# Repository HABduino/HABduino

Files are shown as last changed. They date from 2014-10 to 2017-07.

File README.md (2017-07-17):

## Habduino

This is the original code base for Habduino V4.X boards. It is still suitable for flights but is no longer maintained or supported. Hardware definitions are all current. 

This code provides simultaneous (where legal and supported by the hardware installed) transmission of radio telemetry via RTTY and APRS on Habduino Arduino addon boards for High Altitude Ballooning. 

## Move to Flextrack

We strongly recommend you move to Dave Akermans Flextrack as this is updated and maintained. The Flextrack code is here https://github.com/daveake/FlexTrack and has Habduino specific amendments.

## Disclaimer

The Habduino code is provided as is with no guarantees of performance or operation. 

If you decide to use this code under a balloon it’s your responsibility to ensure you comply with the local legislation and laws regarding meteorological balloon launching and radio transmission in the air. 
The Radiometrix NTX2B 434Mhz is NOT license exempt in the United States of America and does need a radio amateur license.

Use of APRS requires a radio amateur license in all countries and a number of countries don’t permit the airborne use of APRS under any circumstances. 

It is YOUR responsibility to ensure Habduino hardware and code is used safely and legally please review the safety section on the website. 

## Further Reading on High Altitude Ballooning

Please read this http://www.daveakerman.com/?p=1732

## License

The hardware design & code for Habduino is released under a Creative Commons License 3.0 Attribution-ShareAlike License : http://creativecommons.org/licenses/by-sa/3.0/

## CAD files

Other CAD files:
Hardware/HABdunio.skp

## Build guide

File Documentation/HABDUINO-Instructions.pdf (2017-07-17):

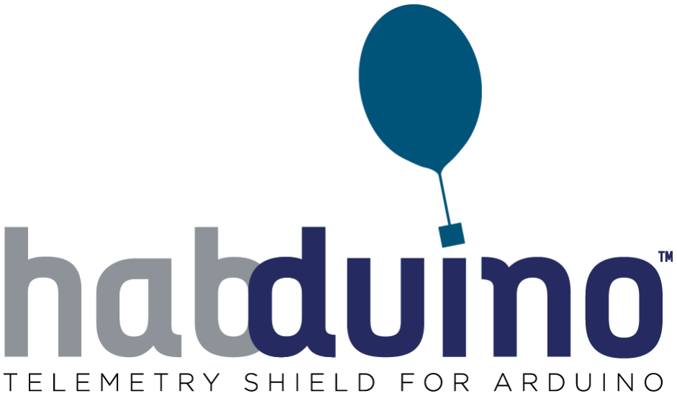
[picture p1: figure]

INSTRUCTION MANUAL

V1.2

Thanks for your purchase of the Habduino Shield.

The Habduino kit is sold as is with no guarantees of performance or operation.

If you decide to use this product under a balloon it’s your responsibility to ensure you comply with the local legislation and laws regarding meteorological balloon launching and radio transmission in the air.

The Radiometrix NTX2B 434Mhz is NOT license exempt in the United States of America and does need a radio amateur license.

Use of APRS requires a radio amateur license in all countries and a number of countries don’t permit the airborne use of APRS under any circumstances.

The Habduino cannot do APRS without an addon Radiometrix HX1 module (See APRS Section).

It is YOUR responsibility to ensure this kit is used safely please review the safety section.

Please read this guide on High Altitude Ballooning. http://www.daveakerman.com/?p=1732

Please note the where supplied RG174 pigtail MUST be turned into a suitable antenna. Instructions to do this are here : http://ukhas.org.uk/guides:payloadantenna

The hardware design & code for Habduino is released under a Creative Commons License 3.0 Attribution-ShareAlike License : http://creativecommons.org/licenses/by-sa/3.0/

The latest code and documentation is available here: https://github.com/HABduino

Kit Contents

Habduino Shield
Battery Holder
Active Patch Antenna
RG174 Pigtail to make an antenna (434MHz kit only)

Introduction

Habduino is compatible with the UKHAS telemetry formats and the APRS network where permitted and where the suitable HX1 module is fitted.

Habduino utilises the latest Ublox MAX M8Q GPS rated for altitudes up to 50km, a 434MHz TCXO equipped frequency agile radio transmitter (where fitted) and/or a Radiometrix HX1 (where fitted) to provide APRS transmissions on 2 meters.

An efficient step up power regulator is fitted that powers both the Arduino and shield from a pair of AA batteries without the need for any further power supplies. The code can simultaneously transmit APRS on 2 meters and RTTY on 434MHz.

Radio modules are factory fitted at time of order.

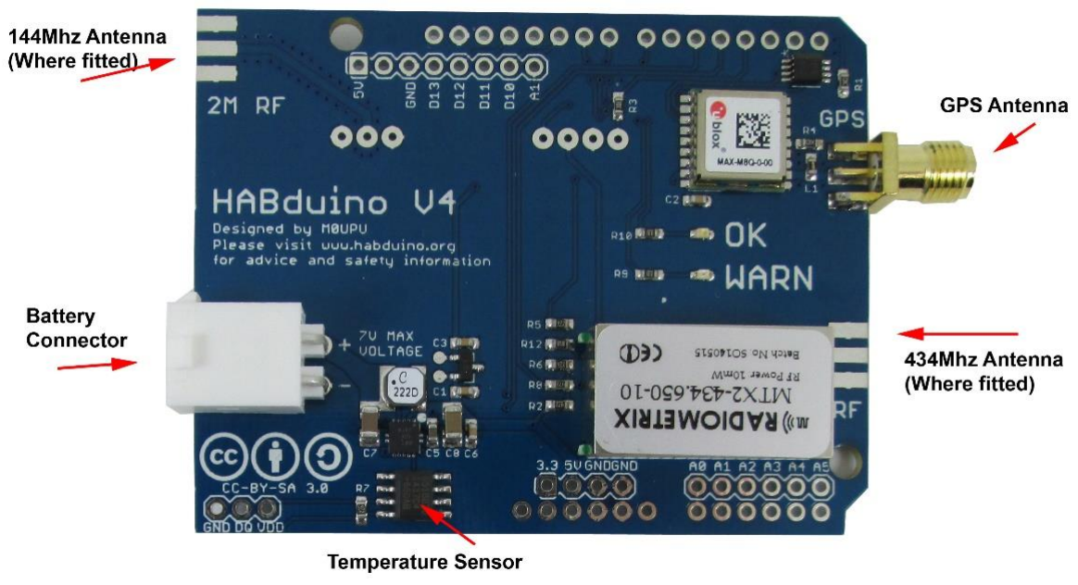
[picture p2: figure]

UKHAS Guidelines
Source : http://ukhas.org.uk/guides:guidelines

This set of guidelines has been put together by members of UKHAS (United Kingdom High Altitude Society) as a recommendation of how to operate high altitude balloon flights safely. They are not legally binding rules however UKHAS do recommend that people follow them as they are based on years of experience in the UK and US. Launching a balloon is your own responsibility and while these rules won't protect you if something was to happen we'd expect that by following them you reduce the risk of any incidents.

Generally permission from your local aviation authority must be obtained for a meteorological balloon flight; this will include a NOTAM for the launch site.

Projects should aim to make their payload as light as possible both for safety but also as this will require less gas saving money and resources. Flights with payload weights below 1Kg should be the norm and payload weights above 2Kg are discouraged.

Keep within the ICAO regulations for light payloads:

- Flights with one or more payload packages should have a combined mass of less than 4 kg.
- A force of less than 230 N is required to separate the suspended payload and parachute from the balloon. (See Note1)
- if any package is 2 kg or more the area density must be below 13 g per square centimetre. (See Note2)
- Payloads should have insulation surrounding the equipment both for maintaining temperature but also providing 'padding' on impact.
- Antenna elements that face down should be flexible - avoid metal rods.
- Before launching a balloon run computer modelled flight predictions (See Section Planning for a launch), postpone launch if there is a high chance of the payload landing in urban areas or near to airports. If the payload is predicated to pass through or near NOTAM'd airspace, Danger or Air Traffic Zones then discuss this with the operator of these areas.
- Always get the landowners permission before attempting to recover a payload.
- As there is a chance that your payload may not be recoverable strive to make it as environmentally friendly as possible.
- Seek help from more experienced UKHAS members when encountering an area outside your comfort zone.
- Follow local regulations when operating and storing compressed gases such as Helium or Hydrogen.

Note1: The force to be applied in a direction parallel to the suspension line.

Note2: The area density is determined by dividing the total mass in grams of the payload package by the area in square centimetres of its smallest surface.

Gas Safety

Compressed gas of any type can be dangerous and it is recommended you take advice from the supplier of the cylinders as to safety precautions. Gas cylinders are sometimes subject to local regulations with regards to transport and storage.
We suggest you review http://www.hse.gov.uk/cdg/pdf/safusgc.pdf for safe handling guidelines of all compressed gas.

Should you choose to use Hydrogen additional safety precautions should be adhered too. It is outside of the scope of this instruction manual to discuss here but as always take safety precautions where necessary and review:
http://ukhas.org.uk/guides:hydrogen
http://arhab.org/pdfs/h2_safety_fsheet.pdf

Batteries

Always uses a fresh set of Energizer Ultimate Lithium batteries when launching. No other battery is suitable or recommended: http://data.energizer.com/PDFs/l91.pdf.

Cameras

It is possible for cheap key ring cameras to lock the GPS module out, ensure these cameras if used are kept away from the GPS antenna.

GPS Antenna

The GPS Antenna should have a clear unobstructed view of the sky. The signals will pass through foam but not through foil.

Hand Warmers

These are not required, the electronics will keep themselves warm.

Predictions

Use the http://habhub.org/calc/ Balloon Burst calculator (Aim for 5.5m/s ascent rate) and http://predict.habhub.org/ to predict the landing spot of your balloon.

Balloons

Balloons, parachutes and other flight hardware can be purchased from www.randomengineering.co.uk

Support and Further Information

If you have any doubts or questions please come speak to us on IRC : http://webchat.freenode.net/?channels=highaltitude

The UKHAS Wiki has lots of information on it : http://ukhas.org.uk/ and will answer many of your questions.

Please read this http://www.daveakerman.com/?p=1732

Getting Started

Hardware

Insert the Habduino shield into your Arduino board. Please note:

Never connect the USB and the external battery pack at the same time.

Screw the GPS antenna firmly onto the GPS SMA connector.

Although the GPS is connected via hardware serial the design means you can program the Arduino as normal without having to remove the shield.

You don’t need an antenna on the 434 MHz radio to test but it may help. You can just insert a single core piece of wire 164mm long into the SMA socket for testing.

Use of an antenna with the HX1 module is mandatory due to the higher output power.

Plug the Arduino into your PC via the USB.

We have noticed some Arduinos, especially the clones have poor regulators, if you are experiencing decoding errors please power the boards from the battery pack. We only recommend the use of genuine Arduino boards.

Getting Started

Software

Download 1.6.5 Arduino IDE from www.arduino.cc

https://www.arduino.cc/en/Main/OldSoftwareReleases#previous

Do not use newer versions of Arduino IDE there seems to be a bug and the code won't run.

Downloading the Latest Firmware

Go to https://github.com/daveake/FlexTrack

Click Clone or Download -> Download ZIP

Extract this to your desktop

Rename the folder these files were extracted too from FlexTrack-master to FlexTrack

Run Arduino 1.6.5

File Open -> Locate FlexTrack.ino

Set your board i.e Arduino Uno in Tools -> Board

Set the boards COM port

Click Sketch -> Include Libraries -> Manage Libraries

Search for Onewire

Select the OneWire by Jim Studt and click install

Search for Dallas

Select the DallasTemperature by Miles Burton and click install Now configure as applicable:

434MHz Operation

Amend line 29 to your RTTY call sign.

#define RTTY_PAYLOAD_ID "HABDUINO" | // Do not use spaces.

2MTR/APRS Operation

Amend line 55 to your APRS call sign (if applicable)

#define APRS_CALLSIGN | "K1ABC" | // Max 6 characters

Press Sketch -> Upload

Operation

Once uploaded at power on the board LED’s should flash rapidly, this is the initialisation period. After a short period the WARN LED should blink once a second until GPS lock has been achieved at which point the blinking red WARN LED should be replaced by a GREEN OK LED blinking.

Occasionally the WARN LED may blink but quickly switch back to GREEN, this is ok.

Once the module detects its above 1000 meters in altitude the LED’s will turn off entirely if you are launching above 1000 meters you can amend the code to stop this.

Below 1000 meters the GPS module is in the more accurate pedestrian mode, above this the code will switch the module to flight mode to ensure it works at high altitude.

The 434Mhz transmissions can be received by any radio capable of reception 434Mhz SSB. RTL dongles work though lack sensitivity, we recommend the Airspy.

There is a guide on receiving and decoding here:

https://ukhas.org.uk/guides:tracking_guide

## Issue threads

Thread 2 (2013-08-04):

Add SD Card Data Logging

Upuaut, 2013-08-04:
Definitely Version 2 of the PCB & Software!

Upuaut, 2015-02-05:
We don't think there is enough memory on the Atmega328P to do this and the rest of the stuff. We breadboarded it and even with the APRS coded removed it wouldn't work. We could start ripping unnecessary stuff out of the library but even then its going to be so tight I doubt we'll be able add any code in the future. To this end we've decided not to implement an SD card natively on the PCB. Sorry folks!

Closed 2015-02-05.

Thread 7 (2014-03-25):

Compile errors on Leonardo

Upuaut, 2014-03-25:
Doesn't compile when Leonardo is selected. Unsure of work around at this time possibly a bug in the Arduino platform rather than the Habduino code.

Upuaut, 2016-01-17:
We have no plans to resolve this issue.

Closed 2016-01-17.

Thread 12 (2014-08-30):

The altitude in RTTY strings is set by "altmax" variable?

rossengeorgiev, 2014-08-30:
This code:
https://github.com/HABduino/HABduino/blob/4f761bcb3b1ebe6875d95b780ed67466d98a066d/Software/habduino/habduino.ino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

Not sure if that's intended or a bug.

hexameron, 2015-02-05:
It is a good feature. "altmax" is reset to zero after every sentence, so Habduino reports the highest altitude at burst. The downside is that the altitude graph clamps to zero when gps lock is <4 sats.
It might be an idea to have a "last_good_altmax" variable to use when altmax is zero.

rossengeorgiev, 2015-02-06:
I'm confused. So, it doesn't record the max achieved altitude, instead is the max altitude received from the gps between transmissions. That's a strange behavior. You could end up in a situation where you get coordinates from the last gps sentence, but the altitude from a sentence before that, which had a higher altitude. Also, you get altitude 0 if there was no lock between transmissions.

Another situation is getting a couple of good positions, and just before you transmit you get a `sat < 4`. You will just send some altitude and `0,0`. Perhaps that's the purpose behind it, but it's seems confusing.

hexameron, 2015-02-06:
You could check the logs, but I think thats what Habduino was doing the last time it flew. Upu uses the same code on his Pava trackers, but they don`t seem to lose GPS lock so it is not an issue there.

hexameron, 2015-02-06:
I was remembering that wrong. The Habduino flight was sending Altitude with no Position. I don`t understand that.

Upuaut, 2015-02-08:
Gosh :) Ok that code is a hang over from the days when we were chasing altitude records. As the radio transmission was interrupt driven the GPS could happily be interrogated 15 times in the time it took to transmit a sentenced @ 50 baud.In that 15 seconds it could have achieved its maximum altitude and burst. obviously when it bursts it drops pretty quickly.

At time there was only 50 meters in the record so the code reports the maximum altitude achieved since the last string was transmitted. Once transmitted it just resets and starts the cycle again.

So to clarify it only reports the maximum altitude achieved during one telemetry transmission. You are correct it could result in a altitude from one location report with the coordinates from another but in reality this doesn't matter. If there is no lock (unusual) the code should report 0,0,0 anyway.

Hope this confirms the behaviour, its probably not needed but people like to know exactly how high they got.

Closed 2015-02-08.

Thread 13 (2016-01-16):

Habduino_V4: 9 December 2015 Version: Does not compile

zs1jen, 2016-01-16:
Error >  gps_ubx_checksum not declared in scope

The problem seems to be resolved by relocating the following routine and commenting it out in its original location.

void gps_ubx_checksum(uint8_t* data, uint8_t len, uint8_t* cka,
uint8_t* ckb)
{
  *cka = 0;
  *ckb = 0;
  for( uint8_t i = 0; i < len; i++ )
  {
    *cka += *data;
    *ckb += *cka;
    data++;
  }
}

bool _gps_verify_checksum(uint8_t* data, uint8_t len)

See attached file.
[habduino_v4.zip](https://github.com/HABduino/HABduino/files/93066/habduino_v4.zip)

I am still learning to program the Arduino so am not sure I have actually got this resolved properly. RTTY prints correctly on screen.  Please verify and assist.

IDE used for compile is 1.6.7

Upuaut, 2016-01-17:
I'll get this checked but I know it compiles fine on older versions.

zs1jen, 2016-01-17:
Thank you. I will try compiling under 1.0.5 and report back.  I may also have a version or two in between 1.05 and 1.6.7

zs1jen, 2016-01-17:
Spot on it does compile as is from the master under 1.0.5

Upuaut, 2016-01-17:
Ok thanks. I'll mark this as closed for the moment. You are welcome to try
Dave Akermans flextrack
https://github.com/daveake/FlexTrack

Its default board is Habduino.

Cheers

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

Closed 2016-01-17.

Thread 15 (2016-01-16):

Habduino_V4: 9 December 2015: RTTY Repetitive TX Glitch

zs1jen, 2016-01-16:
RTTY decode on or about every 5th line transmitted shows the TX shifting frequency.  This results in lost data. See included image.  Arduino Uno R3 powered from lap top.
[Habduino_V4_RTTY_Glitch.zip](https://github.com/HABduino/HABduino/files/93083/Habduino_V4_RTTY_Glitch.zip)
[Habduino_V4_RTTY_Glitch_1.zip](https://github.com/HABduino/HABduino/files/93082/Habduino_V4_RTTY_Glitch_1.zip)

Habduino_v4.ino as attached. The file is the same as submitted for the "Does not compile issue and has the changes included which I made. [habduino_v4.zip](https://github.com/HABduino/HABduino/files/93089/habduino_v4.zip)

Regards
Andre

zs1jen, 2016-01-17:
The problem is related to the power source from USB port on the laptop.

Closed 2016-01-17.

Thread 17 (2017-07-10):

GPS Locking Issues

Laserman, 2017-07-10:
GPS will very rarely acquire a lock, when it does it is not very consistent. This is on the V4.1 board, red light will blink indefinitely, never transmits APRS.

gurlavie, 2017-07-10:
Just from my experience - are yo operating from a battery ?
I found out that when a terry voltage is too low - the system operates, but
no Gps lock, or the lock is acquired for a very short time.

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

Upuaut, 2017-07-10:
No/long lock times aren't a coding issue indicating some other issue with the hardware. As Gur advises please run from battery also please try another antenna. If you suspect the hardware is faulty please contact Uputronics to discuss.

Closed 2017-07-10.

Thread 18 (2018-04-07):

I can't locate HABDUINO

origovi, 2018-04-07:
Hi,
I recently bought a HABDUINO v4.1 to track a balloon, but I am not able to found where it is. I use the APRS callsign that a friend led me use (EA3XXX-1), and I use aprs.fi to locate it, but it doesn't appear, I'm pretty sure it's a problem of coding (FlexTrack), I wrote on APRS_CALLSIGN EA3XXX and at SSID 1.

If someone has solved this issue or knows how to solve it, i need help.
Thank you.

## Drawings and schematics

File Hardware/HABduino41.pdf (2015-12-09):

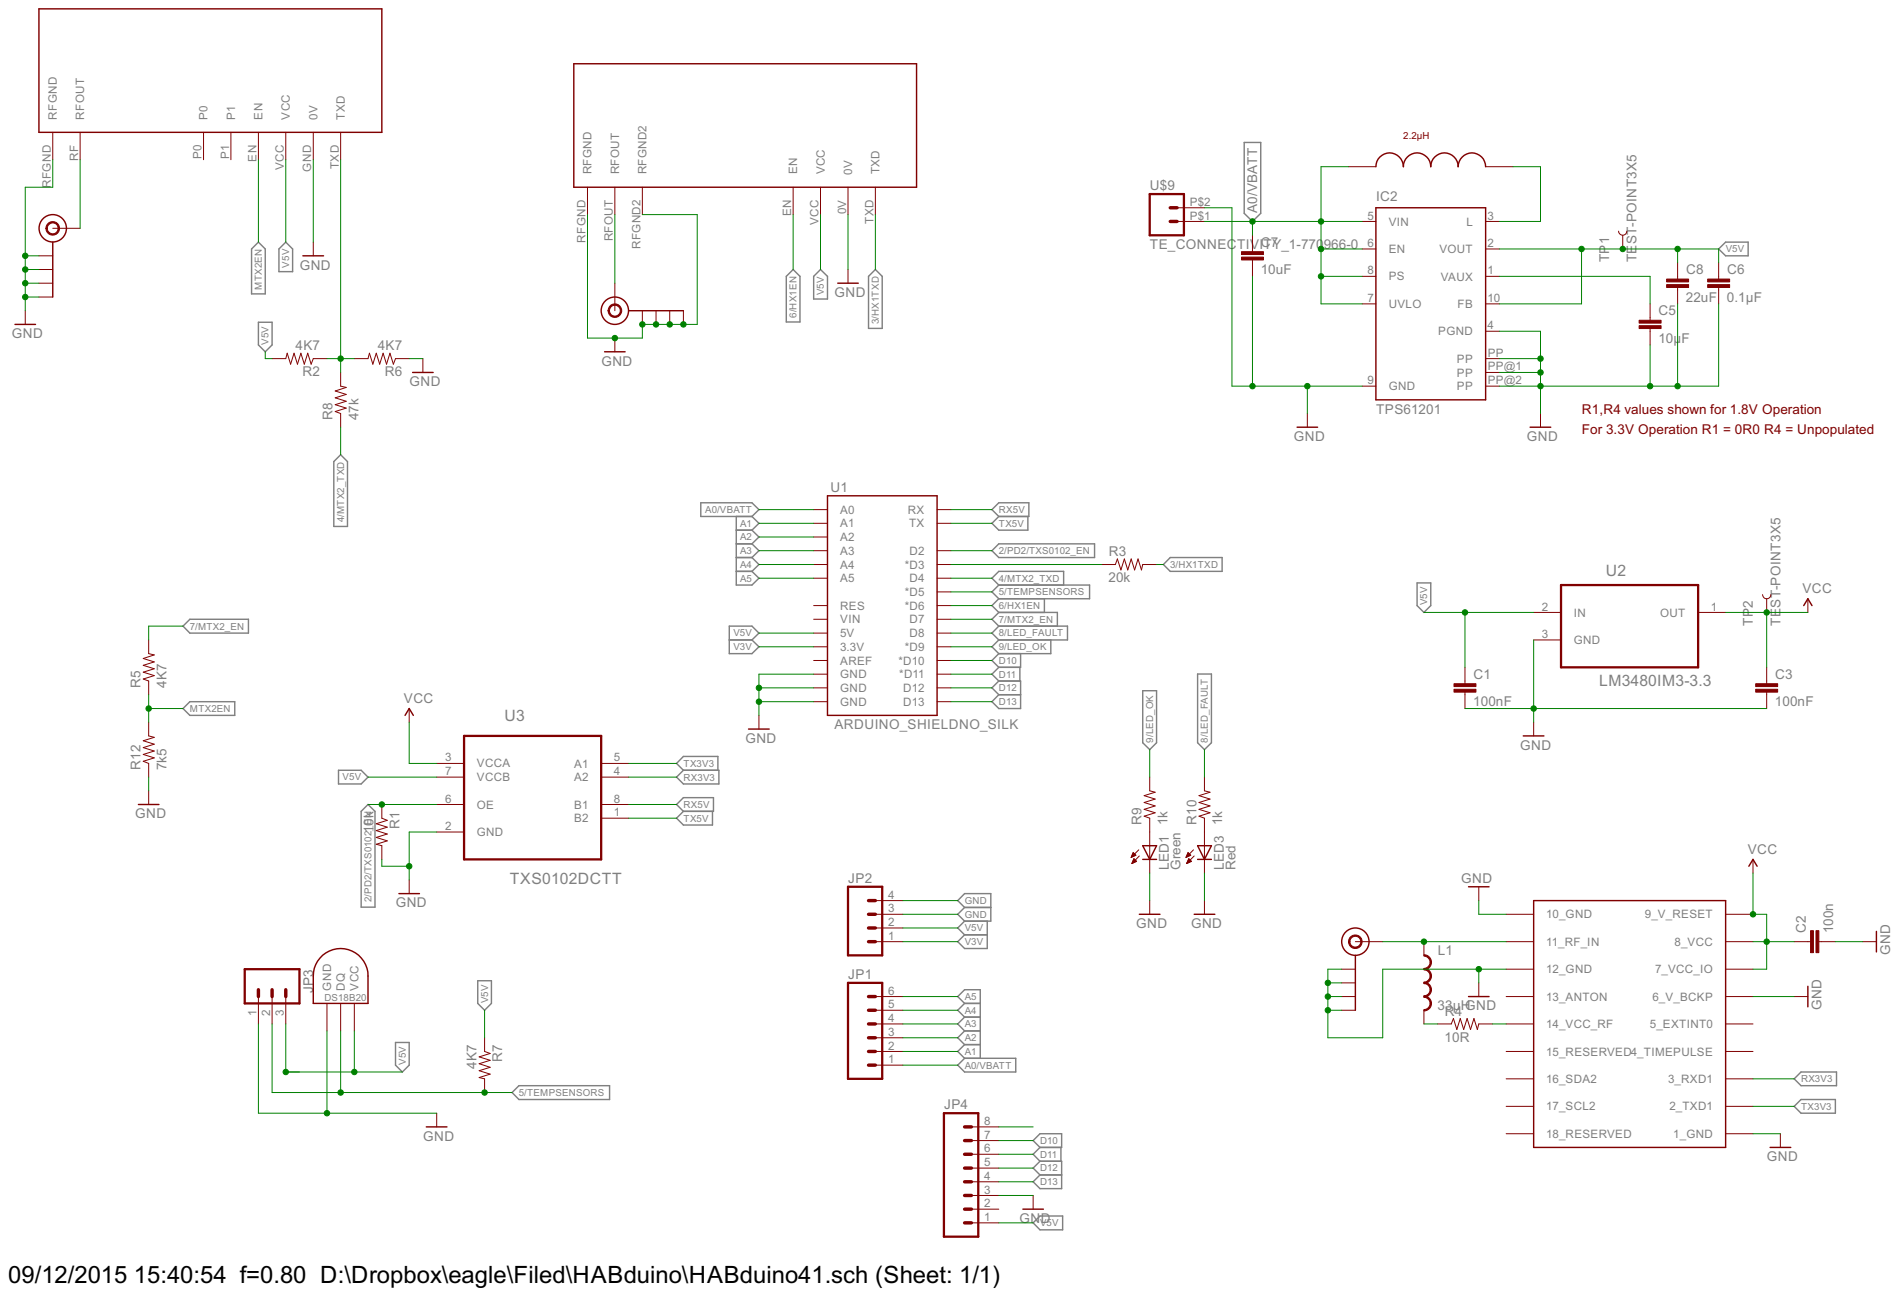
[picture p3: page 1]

R1,R4 values shown for 1.8V Operation For 3.3V Operation R1 = 0R0 R4 = Unpopulated

09/12/2015 15:40:54 f=0.80 D:\Dropbox\eagle\Filed\HABduino\HABduino41.sch (Sheet: 1/1)

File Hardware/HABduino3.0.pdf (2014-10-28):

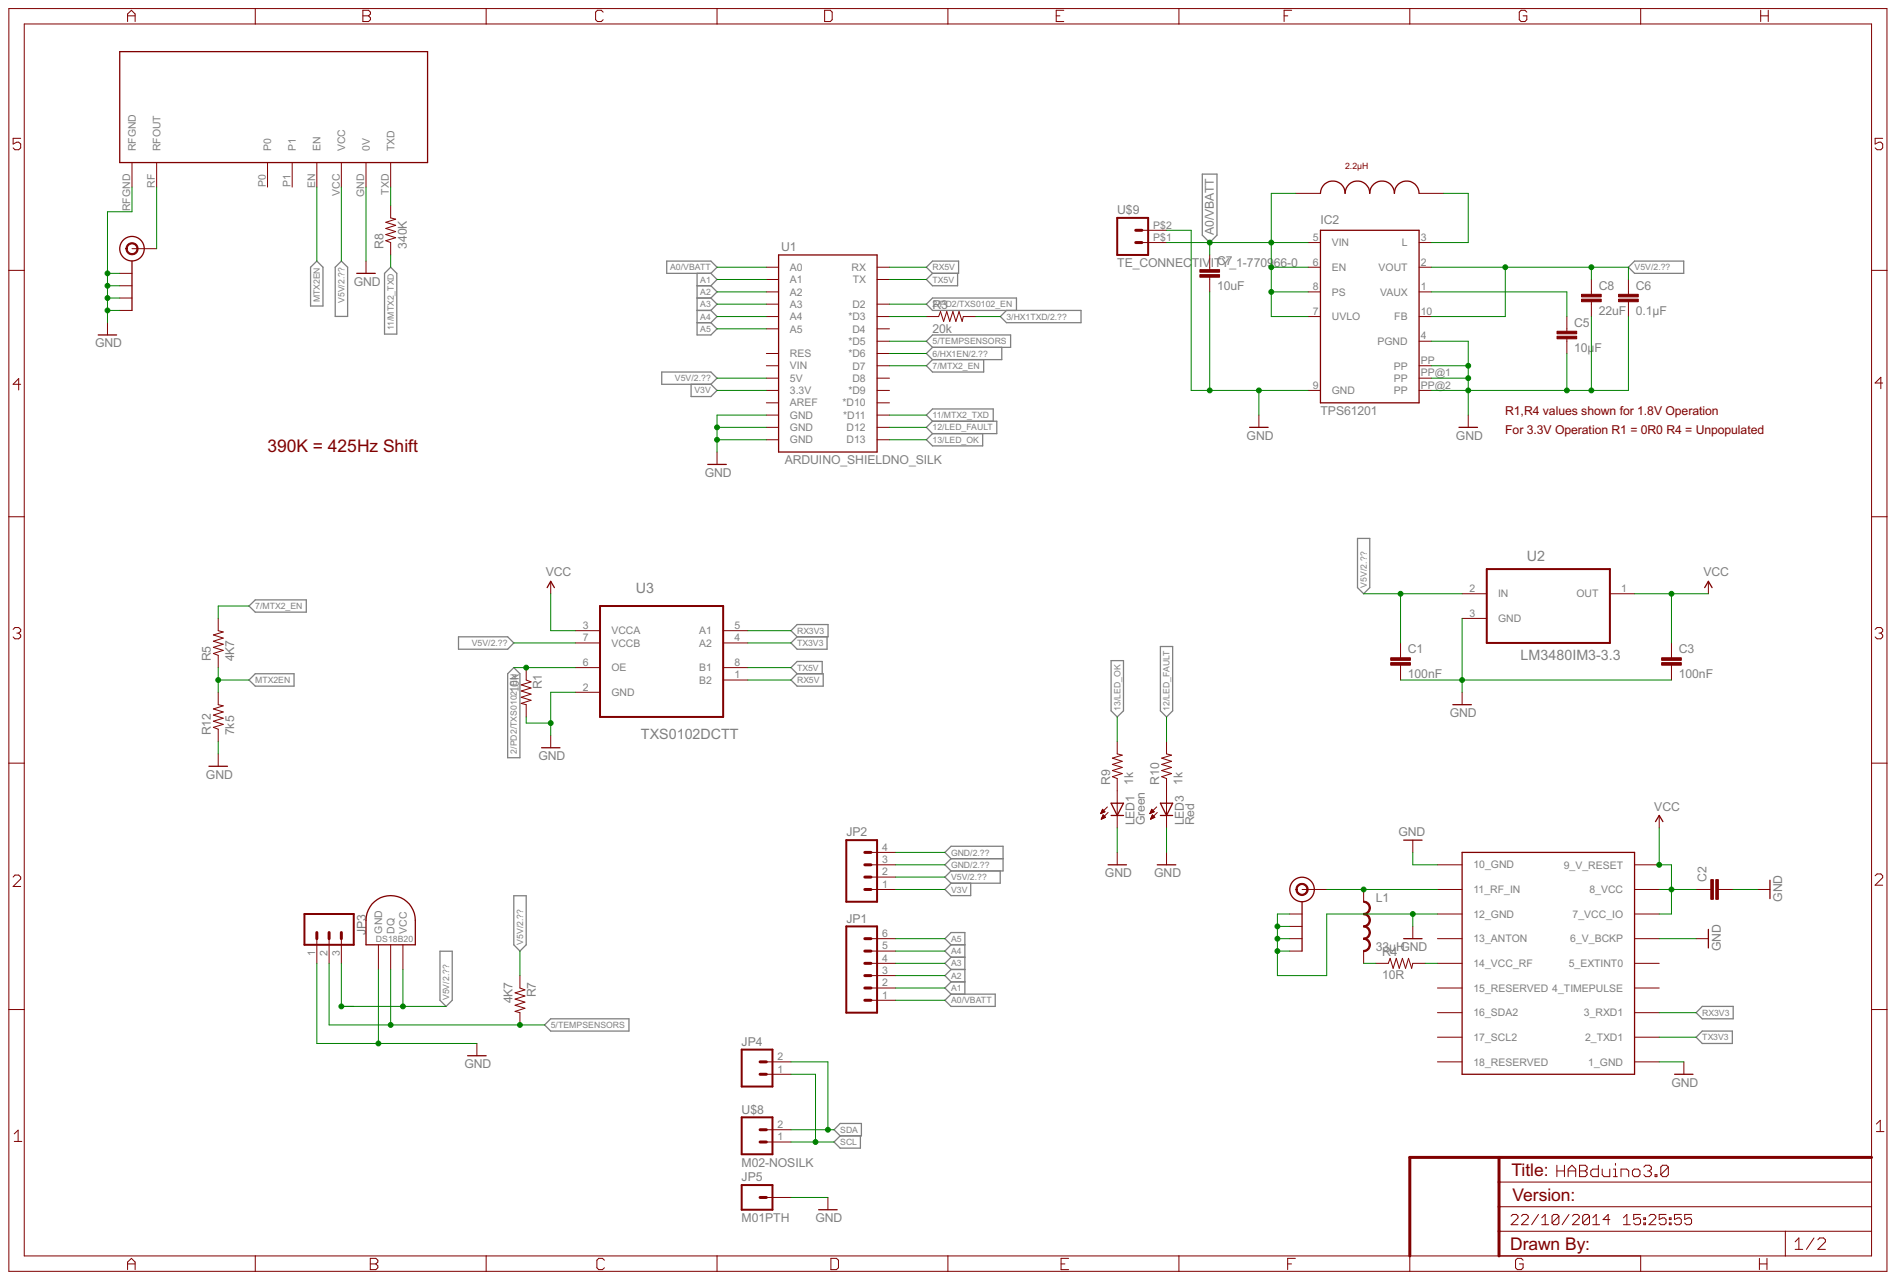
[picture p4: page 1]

Drawn By: Title: Version:

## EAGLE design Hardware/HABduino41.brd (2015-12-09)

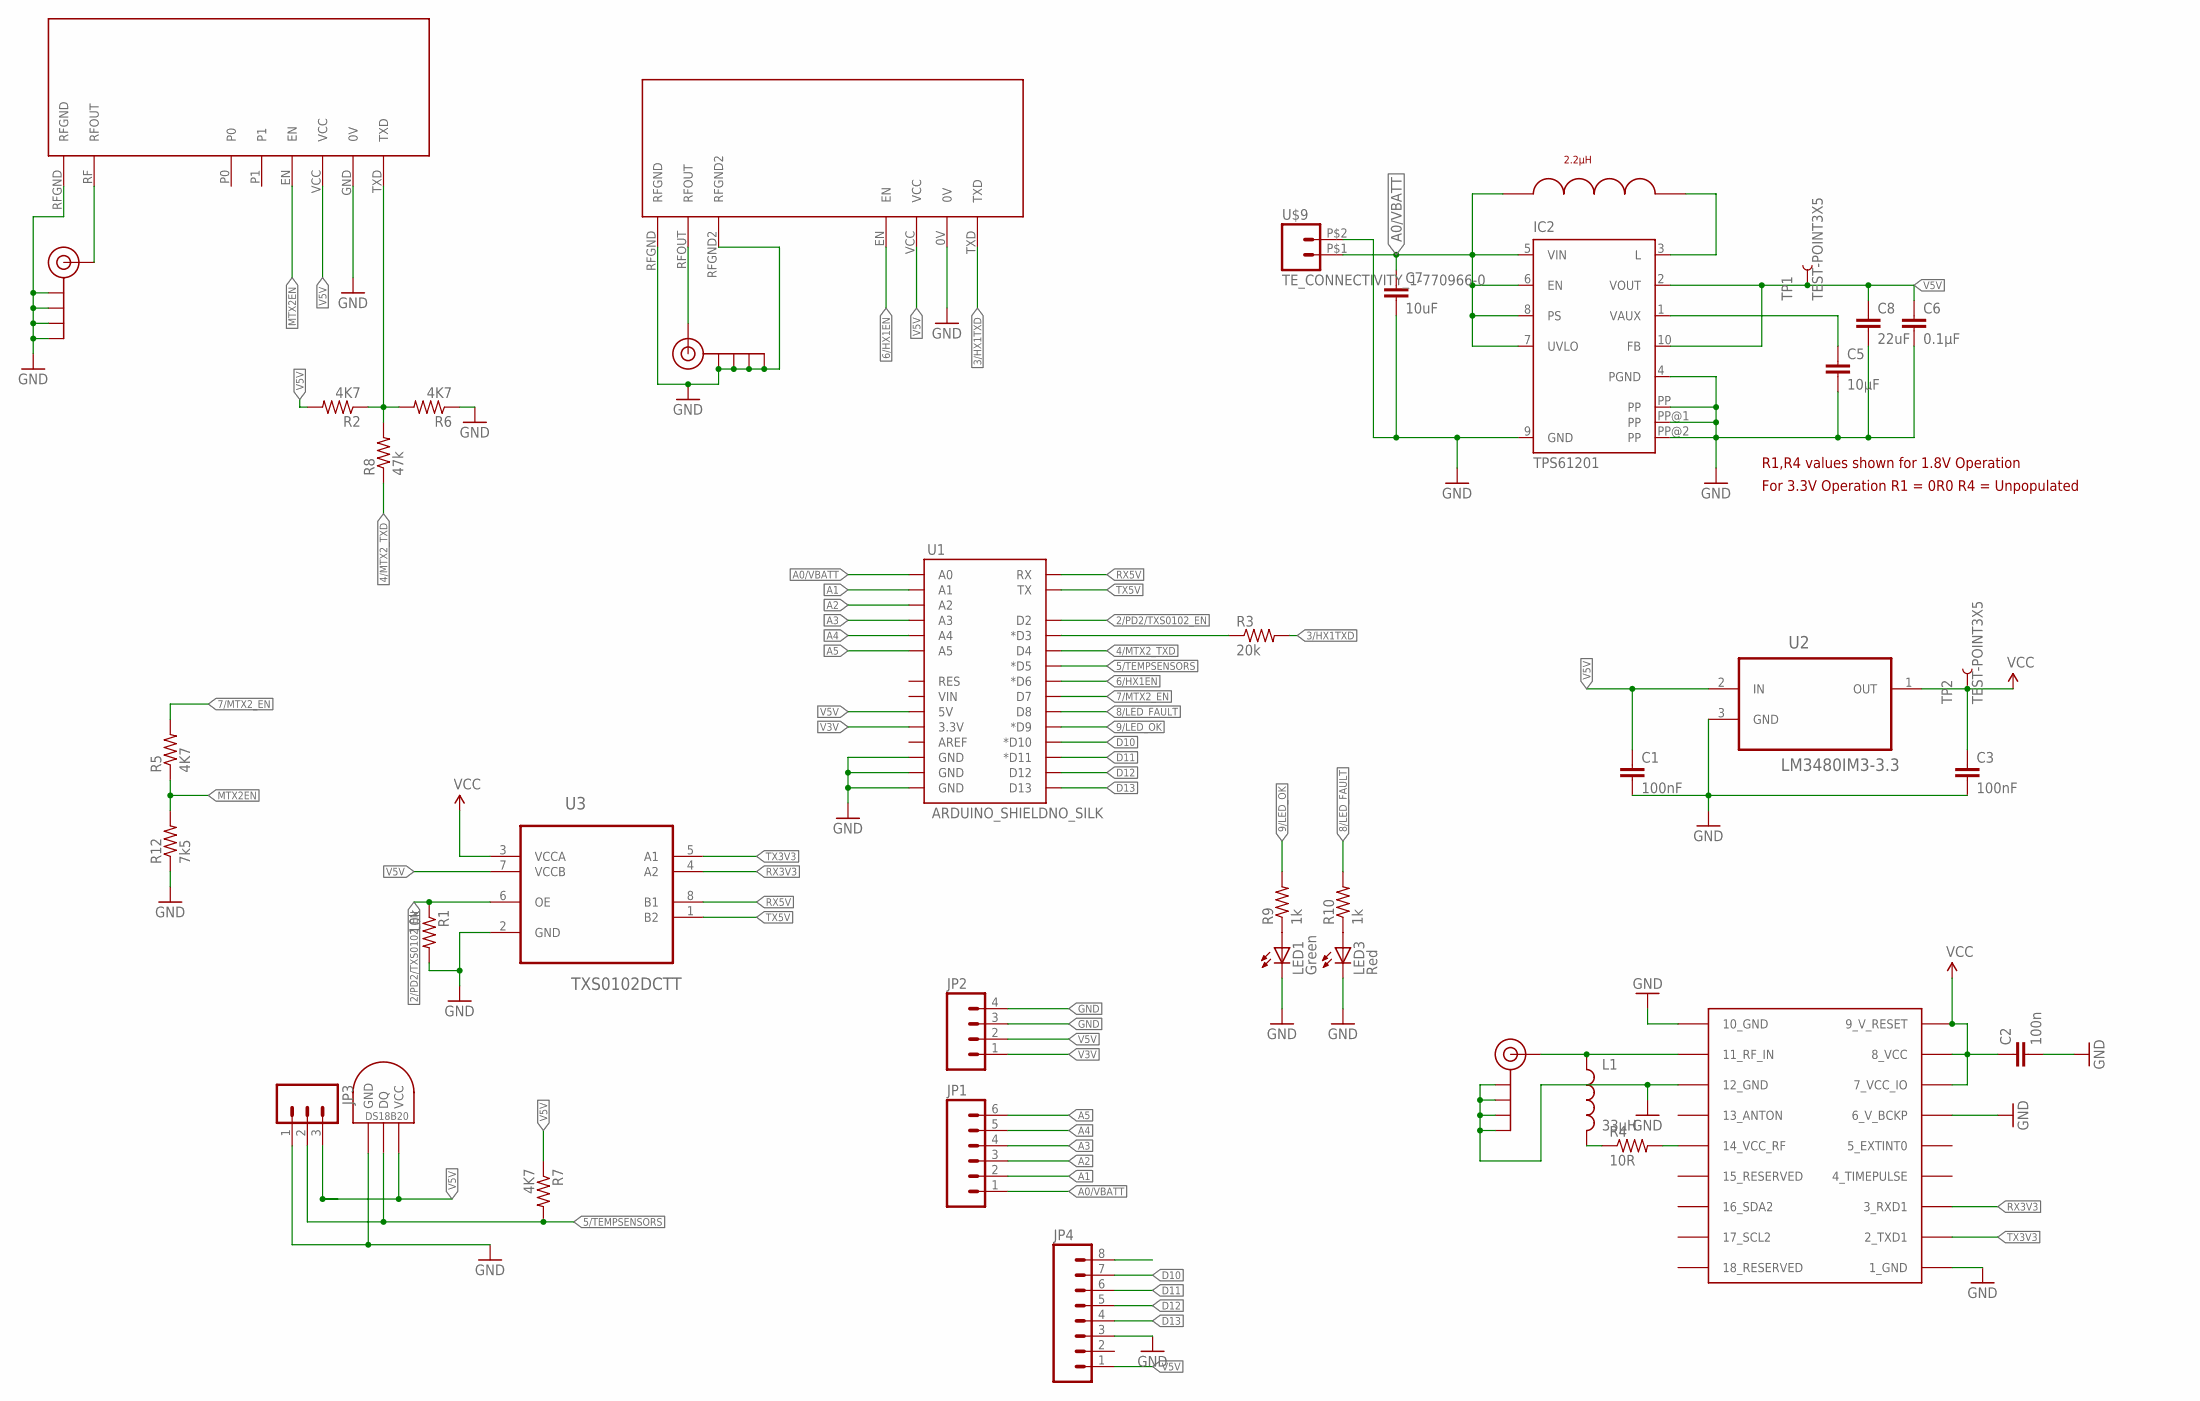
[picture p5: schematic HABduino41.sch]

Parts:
C1, C3: 100nF; 0603-CAP
C2: 100n; 0603-CAP
C5: 10µF; 0603-CAP
C6: 0.1µF; 0603-CAP
C7: 10uF; 1206
C8: 22uF; 1206
IC2: TPS61201; S-PDSO-N10
J$1, J$2, J$4: SMA_EDGE; SMA-EDGE
JP1: M06SIP; 1X06
JP2: M04PTH; 1X04
JP3: M03PTH; 1X03
JP4: M081X08; 1X08
L1: 33µH; 0603
LED1: Green; LED-0603
LED3: Red; LED-0603
LPS4018: 2.2µH; COILCRAFT_LPS4018
R1: 10k; 0603-RES
R2, R5, R6, R7: 4K7; 0603-RES
R3: 20k; 0603-RES
R4: 10R; 0603-RES
R8: 47k; 0603-RES
R9, R10: 1k; 0603-RES
R12: 7k5; 0603-RES
TEMP: DS1821; DS18B20_SOIC
TP1, TP2: TEST-POINT3X5; PAD.03X.05
U1: ARDUINO_SHIELDNO_SILK; DUEMILANOVE_VIAS
U2: LM3480IM3-3.3; SOT95P251X112-3N
U3: TXS0102DCTT; SOP65P400X130-8N
U$1: UBLOX_MAX
U$2: RADIOMETRIX-HX1
U$4: RADIOMETRIX-MTX2
U$9: TE_CONNECTIVITY_1-770966-0; FARNELL 1098556

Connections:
2/PD2/TXS0102_EN: R1.1, U1.D2, U3.6 (OE)
3/HX1TXD: R3.2, U$2.TXD
4/MTX2_TXD: R8.1, U1.D4
5/TEMPSENSORS: JP3.2, R7.2, TEMP.DQ, U1.D5 (*D5)
6/HX1EN: U1.D6 (*D6), U$2.EN
7/MTX2_EN: R5.2, U1.D7
8/LED_FAULT: R10.2, U1.D8
9/LED_OK: R9.2, U1.D9 (*D9)
A0/VBATT: C7.1, IC2.5 (VIN), IC2.6 (EN), IC2.7 (UVLO), IC2.8 (PS), JP1.1, LPS4018.P$1, U1.A0, U$9.P$1 (1)
A1: JP1.2, JP4.8, U1.A1
A2: JP1.3, U1.A2
A3: JP1.4, U1.A3
A4: JP1.5, U1.A4
A5: JP1.6, U1.A5
D10: JP4.7, U1.D10 (*D10)
D11: JP4.6, U1.D11 (*D11)
D12: JP4.5, U1.D12
D13: JP4.4, U1.D13
GND: C1.2, C2.2, C3.2, C5.2, C6.2, C7.2, C8.2, IC2.4 (PGND), IC2.9 (GND), IC2.PP, IC2.PP@1 (PP), IC2.PP@2 (PP), J$1.GND@0 (GND), J$1.GND@1 (GND), J$1.GND@2 (GND), J$1.GND@3 (GND), J$2.GND@0 (GND), J$2.GND@1 (GND), J$2.GND@2 (GND), J$2.GND@3 (GND), J$4.GND@0 (GND), J$4.GND@1 (GND), J$4.GND@2 (GND), J$4.GND@3 (GND), JP2.3, JP2.4, JP3.1, JP4.3, LED1.C, LED3.C, R1.2, R6.1, R12.1, TEMP.GND, U1.GND@0 (GND), U1.GND@1 (GND), U1.GND@2 (GND), U2.3 (GND), U3.2 (GND), U$1.1_GND, U$1.6_V_BCKP, U$1.10_GND, U$1.12_GND, U$2.0V, U$2.RFGND, U$2.RFGND2, U$4.GND (0V), U$4.RFGND, U$9.P$2 (2)
MTX2EN: R5.1, R12.2, U$4.EN
unnamed: R3.1, U1.D3 (*D3)
unnamed: J$1.SIG (SIGNAL), U$4.RF (RFOUT)
unnamed: J$2.SIG (SIGNAL), L1.1, U$1.11_RF_IN
unnamed: IC2.3 (L), LPS4018.P$2
unnamed: J$4.SIG (SIGNAL), U$2.RFOUT
unnamed: R2.1, R6.2, R8.2, U$4.TXD
unnamed: C5.1, IC2.1 (VAUX)
unnamed: LED1.A, R9.1
unnamed: LED3.A, R10.1
unnamed: L1.2, R4.1
unnamed: R4.2, U$1.14_VCC_RF
RX3V3: U3.4 (A2), U$1.3_RXD1
RX5V: U1.RX, U3.8 (B1)
TX3V3: U3.5 (A1), U$1.2_TXD1
TX5V: U1.TX, U3.1 (B2)
V3V: JP2.1, U1.3.3V
V5V: C1.1, C6.1, C8.1, IC2.2 (VOUT), IC2.10 (FB), JP2.2, JP3.3, JP4.1, R2.2, R7.1, TEMP.VCC, TP1.P$1, U1.5V, U2.2 (IN), U3.7 (VCCB), U$2.VCC, U$4.VCC
VCC: C2.1, C3.1, TP2.P$1, U2.1 (OUT), U3.3 (VCCA), U$1.7_VCC_IO, U$1.8_VCC, U$1.9_V_RESET

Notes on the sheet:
R1,R4 values shown for 1.8V Operation
For 3.3V Operation R1 = 0R0 R4 = Unpopulated

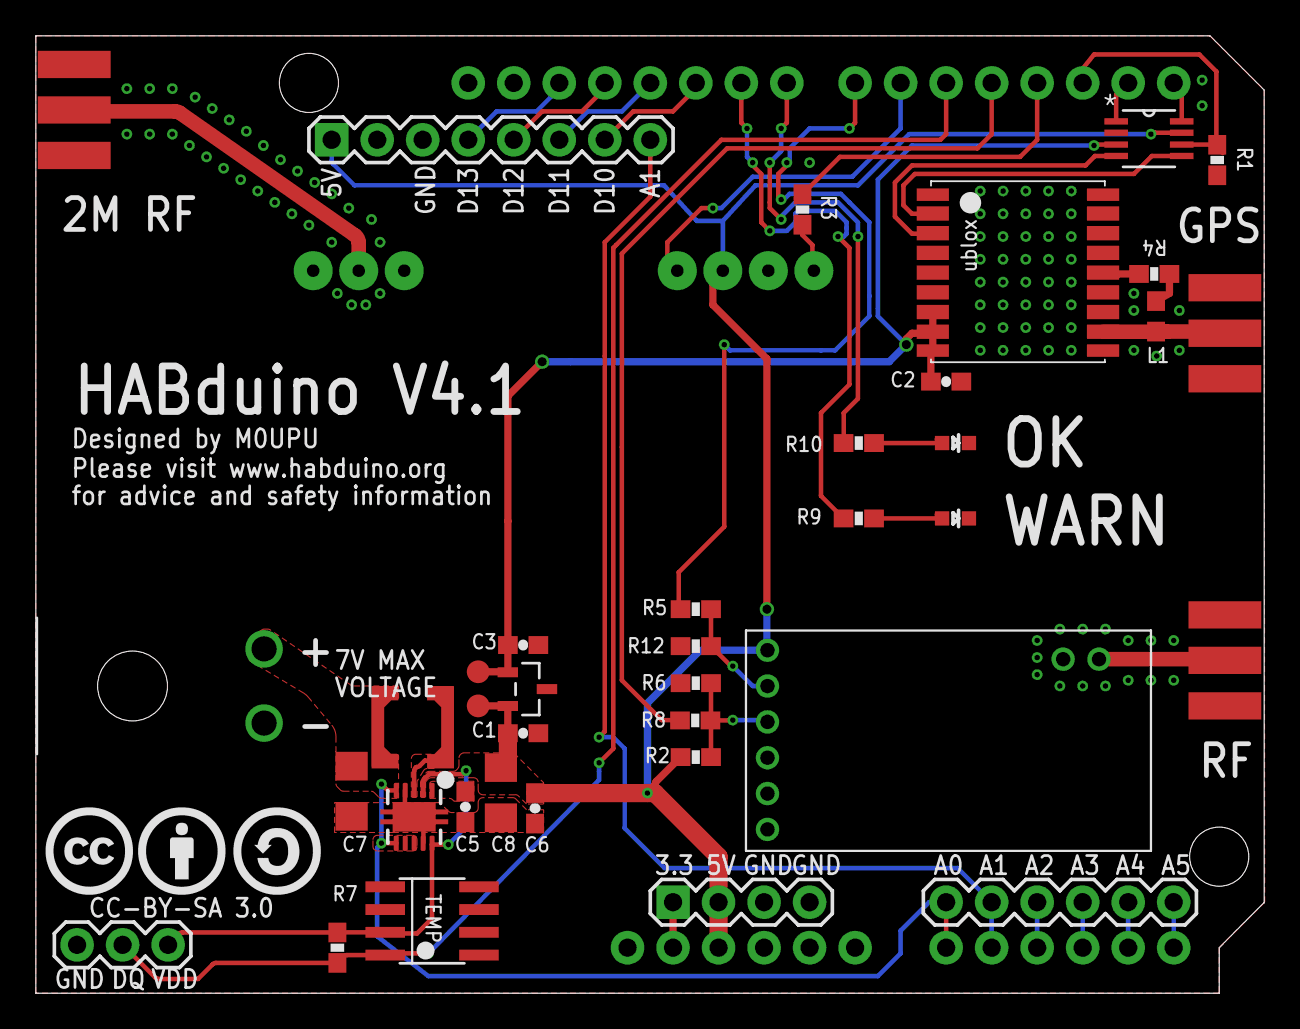
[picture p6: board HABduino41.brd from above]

Board: 2 copper layers, 68.5 x 53.4 mm, 43 parts (1 on the bottom side), 38 nets.

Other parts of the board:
U$3: CC
U$5: CC-BY-21
U$6: CC-SA-21

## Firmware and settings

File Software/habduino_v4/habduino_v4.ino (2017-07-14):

/*
 HABDuino Tracker
 http://www.habduino.org
 (c) Anthony Stirk M0UPU 
 
 March 2015 Version 4.0.1
 
 This is for the Version 4 Habduino Hardware.
 
 Credits :
 
 Interrupt Driven RTTY Code : Evolved from Rob Harrison's RTTY Code.
 Thanks to :  http://www.engblaze.com/microcontroller-tutorial-avr-and-arduino-timer-interrupts/
 http://gammon.com.au/power
 
 Suggestion to lock variables when making the telemetry string & Compare match register calculation from Phil Heron.
 APRS Code mainly by Phil Heron MI0VIM
 
 GPS Code modified from jonsowman and Joey flight computer CUSF
 https://github.com/cuspaceflight/joey-m/tree/master/firmware
 
 Thanks to :
 
 Phil Heron
 James Coxon
 Dave Akerman
 
 The UKHAS Community http://ukhas.org.uk
 
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
 See <http://www.gnu.org/licenses/>.
 
 The Habduino kit is supplied as is with no guarantees of performance or operation. Although the HABDuino 
 is designed for short-term Near Space operation, the conditions may exceed the specification of individual 
 components which may fail to operate correctly because of low temperatures or pressures of increased 
 radiation levels. We have no control over the effectiveness of your payload design especially the 
 temperature and electromagnetic conditions  within, thus we make no warrnaty express or implied as to
 the ability of our products to operate to any degree of effectiveness when used in your application.
 
 If you decide to use this product under a balloon it’s your responsibility to ensure you comply with the 
 local legislation and laws regarding meteorological balloon launching and radio transmission in the air. 
 
 The Radiometrix MTX2 434Mhz is NOT license exempt in the United States of America and does need a radio
 amateur license.  Use of APRS requires a radio amateur license in all countries and a number of countries 
 don’t permit the airborne use of APRS under any circumstances.  
 The Habduino cannot do APRS without an addon Radiometrix HX1 module.
 
 The hardware design & code for Habduino is released under a Creative Commons License 3.0 Attribution-ShareAlike License :
 See : http://creativecommons.org/licenses/by-sa/3.0/
 It is YOUR responsibility to ensure this kit is used safely please review the safety section.
 
 The latest code is available here : https://github.com/HABduino/HABduino
 
 
 */

/* BITS YOU WANT TO AMEND */

#define MTX2_FREQ 434.485 // format 434.XXX  
char callsign[10] = "CHANGEME";  // MAX 9 CHARACTERS!!

/* BELOW HERE YOU PROBABLY DON'T WANT TO BE CHANGING STUFF */

#include <util/crc16.h>
#include <avr/io.h>
#include <avr/interrupt.h>
#include <avr/pgmspace.h>
#include <OneWire.h>
#include <DallasTemperature.h>
#include <SoftwareSerial.h>
#include "ax25modem.h"
static const uint8_t PROGMEM _sine_table[] = {
#include "sine_table.h"
};
#define ASCII 7          // ASCII 7 or 8
#define STOPBITS 2       // Either 1 or 2
#define TXDELAY 0        // Delay between sentence TX's
#define RTTY_BAUD 50     // RTTY Baud rate (Recommended = 50)
#define LED_WARN 9
#define LED_OK 8
#define BATTERY_ADC A0
//#define MTX2_SHIFT 425        
//#define MTX2_OFFSET 0          // 0-100 Slightly adjusts the frequency by increasing the PWM 
#define MTX2_TXD 4
#define MTX2_ENABLE 7


#define HX1_ENABLE 6
#define HX1_TXD 3
#define GPS_ON 2
#define POWERSAVING
#define ONE_WIRE_BUS 5
#define ONE_SECOND F_CPU / 1024 / 16


#define BAUD_RATE      (1200)
#define TABLE_SIZE     (512)
#define PREAMBLE_BYTES (50)
#define REST_BYTES     (5)

#define PLAYBACK_RATE    (F_CPU / 256)
#define SAMPLES_PER_BAUD (PLAYBACK_RATE / BAUD_RATE)
#define PHASE_DELTA_1200 (((TABLE_SIZE * 1200L) << 7) / PLAYBACK_RATE)
#define PHASE_DELTA_2200 (((TABLE_SIZE * 2200L) << 7) / PLAYBACK_RATE)
#define PHASE_DELTA_XOR  (PHASE_DELTA_1200 ^ PHASE_DELTA_2200)

SoftwareSerial MTX2_EN(12, MTX2_ENABLE); // RX, TX
OneWire oneWire(ONE_WIRE_BUS);
DallasTemperature sensors(&oneWire);

volatile int txstatus=1;
volatile int txstringlength=0;
volatile char txc;
volatile int txi;
volatile int txj;
volatile int count=1;
volatile boolean lockvariables = 0;
volatile static uint8_t *_txbuf = 0;
volatile static uint8_t  _txlen = 0;

int errorstatus=0;
/* Error Status Bit Level Field :
 Bit 0 = GPS Error Condition Noted Switch to Max Performance Mode
 Bit 1 = GPS Error Condition Noted Cold Boot GPS
 Bit 2 = DS18B20 temp sensor status 0 = OK 1 = Fault
 Bit 3 = Current Dynamic Model 0 = Flight 1 = Pedestrian
 Bit 4 = PSM Status 0 = PSM On 1 = PSM Off                   
 Bit 5 = Lock 0 = GPS Locked 1= Not Locked
 
 So error 8 means the everything is fine just the GPS is in pedestrian mode. 
 Below 1000 meters the code puts the GPS in the more accurate pedestrian mode. 
 Above 1000 meters it switches to dynamic model 6 i.e flight mode and turns the LED's off for additional power saving. 
 So as an example error code 40 = 101000 means GPS not locked and in pedestrian mode. 
 */

char txstring[100];
uint8_t buf[60]; 
uint8_t lock =0, sats = 0, hour = 0, minute = 0, second = 0;
uint8_t oldhour = 0, oldminute = 0, oldsecond = 0;
int GPSerror = 0,navmode = 0,psm_status = 0,lat_int=0,lon_int=0,tempsensors,temperature1=0,temperature2=0;
int32_t lat = 0, lon = 0, alt = 0, maxalt = 0, lat_dec = 0, lon_dec =0 ,tslf=0;
unsigned long currentMillis;
long previousMillis = 0;
int batteryadc_v,battvaverage=0,aprstxstatus=0; 
int32_t battvsmooth[5] ;
int aprs_tx_status = 0, aprs_attempts = 0;
unsigned long startTime;
char comment[3]={
  ' ', ' ', '\0'};


void setup()  { 
  pinMode(MTX2_TXD, OUTPUT);
  pinMode(LED_WARN, OUTPUT);
  pinMode(HX1_ENABLE, OUTPUT);
  pinMode(LED_OK,OUTPUT);
  pinMode(MTX2_ENABLE, OUTPUT);
  pinMode(GPS_ON, OUTPUT);
  pinMode(BATTERY_ADC, INPUT);
  blinkled(6);
  setMTX2Frequency();
  Serial.begin(9600);
  digitalWrite(MTX2_ENABLE,HIGH);
  blinkled(5);
  digitalWrite(GPS_ON,HIGH);
  blinkled(4);
  resetGPS();
  blinkled(3);

#ifndef APRS
  TCCR2B = TCCR2B & 0b11111000 | 1; // Sets fast PWM on pin 11
#endif

#ifdef APRS
  ax25_init();
#endif

  blinkled(2);
  setupGPS();
  blinkled(1);
  initialise_interrupt();
  sensors.begin();
  tempsensors=sensors.getDeviceCount();
} 

void loop()   {
  oldhour=hour;
  oldminute=minute;
  oldsecond=second;
  gps_check_nav();

  if(lock!=3) // Blink LED to indicate no lock
  {
    errorstatus |=(1 << 5);  // Set bit 5 (Lock 0 = GPS Locked 1= Not Locked)
  }
  else
  {
    errorstatus &= ~(1 << 5); // Unset bit 5 (Lock 0 = GPS Locked 1= Not Locked)
  }
  checkDynamicModel();

#ifdef APRS 
  if(sats>=4){
    if (aprs_tx_status==0)
    {
      startTime=millis();
      aprs_tx_status=1;
    }
    if(millis() - startTime > (APRS_TX_INTERVAL*60000)) {
      aprs_tx_status=0;
      send_APRS();
      aprs_attempts++;
    }
  }  
#endif


#ifdef POWERSAVING
  if((lock==3) && (psm_status==0) && (sats>=5) &&((errorstatus & (1 << 0))==0)&&((errorstatus & (1 << 1))==0)) // Check we aren't in an error condition
  {
    setGPS_PowerSaveMode();
    wait(1000);
    psm_status=1;
    errorstatus &= ~(1 << 4); // Set Bit 4 Indicating PSM is on
  }
#endif
  if(!lockvariables) {

    prepare_data();
    if(alt>maxalt && sats >= 4)
    {
      maxalt=alt;
    }
  }
  if((oldhour==hour&&oldminute==minute&&oldsecond==second)||sats<=4) {
    tslf++;
  }
  else
  {
    tslf=0;
    errorstatus &= ~(1 << 0); // Unset bit 0 (Clear GPS Error Condition Noted Switch to Max Performance Mode)
    errorstatus &= ~(1 << 1); // Unset bit 1 (Clear GPS Error Condition Noted Cold Boot GPS)
  }
  if((tslf>10 && ((errorstatus & (1 << 0))==0)&&((errorstatus & (1 << 1))==0))) {
    setupGPS();
    wait(125);
    setGps_MaxPerformanceMode();
    wait(125);
    errorstatus |=(1 << 0); // Set Bit 1 (GPS Error Condition Noted Switch to Max Performance Mode)
    psm_status=0;
    errorstatus |=(1 << 4); // Set Bit 4 (Indicate PSM is disabled)
  }
  if(tslf>100 && ((errorstatus & (1 << 0))==1)&&((errorstatus & (1 << 1))==0)) {
    errorstatus |=(1 << 0); // Unset Bit 0 we've already tried that didn't work
    errorstatus |=(1 << 1); // Set bit 1 indicating we are cold booting the GPS
    Serial.flush();
    resetGPS();
    wait(125);
    setupGPS();
  }
}

void initialise_interrupt() 
{
  // initialize Timer1
  cli();          // disable global interrupts
  TCCR1A = 0;     // set entire TCCR1A register to 0
  TCCR1B = 0;     // same for TCCR1B
  OCR1A = F_CPU / 1024 / RTTY_BAUD - 1;  // set compare match register to desired timer count:
  TCCR1B |= (1 << WGM12);   // turn on CTC mode:
  // Set CS10 and CS12 bits for:
  TCCR1B |= (1 << CS10);
  TCCR1B |= (1 << CS12);
  // enable timer compare interrupt:
  TIMSK1 |= (1 << OCIE1A);
  sei();          // enable global interrupts
}

ISR(TIMER1_COMPA_vect)
{

  if(alt>1000 && sats >= 4)
  {
    digitalWrite(LED_WARN,LOW);  
    digitalWrite(LED_OK,LOW);  
  }
  else 
  {
    currentMillis = millis();
    if(currentMillis - previousMillis > ONE_SECOND) 
    {
      previousMillis = currentMillis;   
      if(errorstatus!=8)
      {
        digitalWrite(LED_WARN,!digitalRead(LED_WARN));
        digitalWrite(LED_OK,LOW);  
      }
      else 
      {
        digitalWrite(LED_OK, !digitalRead(LED_OK)); 
        digitalWrite(LED_WARN,LOW);    
      }
    }
  }

  switch(txstatus) {
  case 0: // This is the optional delay between transmissions.
    txj++;
    if(txj>(TXDELAY*RTTY_BAUD)) { 
      txj=0;
      txstatus=1;
    }
    break;
  case 1: // Initialise transmission
    if(alt>maxalt && sats >= 4)
    {
      maxalt=alt;
    }
    lockvariables=1;
#ifndef APRS
    if(tempsensors==1)
    {
      snprintf(txstring,100, "$$$$$%s,%i,%02d:%02d:%02d,%s%i.%06ld,%s%i.%06ld,%ld,%d,%i,%i,%02x",callsign,count, hour, minute, second,lat < 0 ? "-" : "",lat_int,lat_dec,lon < 0 ? "-" : "",lon_int,lon_dec, maxalt,sats,temperature1,battvaverage,errorstatus);
    }
    else
    {
      snprintf(txstring,100, "$$$$$%s,%i,%02d:%02d:%02d,%s%i.%06ld,%s%i.%06ld,%ld,%d,%i,%i,%i,%02x",callsign,count, hour, minute, second,lat < 0 ? "-" : "",lat_int,lat_dec,lon < 0 ? "-" : "",lon_int,lon_dec, maxalt,sats,temperature1,temperature2,battvaverage,errorstatus);
    }
#endif
#ifdef APRS
    if(tempsensors==1)
    {
      snprintf(txstring,100, "$$$$$%s,%i,%02d:%02d:%02d,%s%i.%06ld,%s%i.%06ld,%ld,%d,%i,%i,%i,%02x",callsign,count, hour, minute, second,lat < 0 ? "-" : "",lat_int,lat_dec,lon < 0 ? "-" : "",lon_int,lon_dec, maxalt,sats,temperature1,battvaverage,aprs_attempts,errorstatus);
    }
    else
    {
      snprintf(txstring,100, "$$$$$%s,%i,%02d:%02d:%02d,%s%i.%06ld,%s%i.%06ld,%ld,%d,%i,%i,%i,%i,%02x",callsign,count, hour, minute, second,lat < 0 ? "-" : "",lat_int,lat_dec,lon < 0 ? "-" : "",lon_int,lon_dec, maxalt,sats,temperature1,temperature2,battvaverage,aprs_attempts,errorstatus);
    }
#endif
    crccat(txstring);
    maxalt=0;
    lockvariables=0;
    txstringlength=strlen(txstring);
    txstatus=2;
    txj=0;
    break;

  case 2: // Grab a char and lets go transmit it. 
    if ( txj < txstringlength)
    {
      txc = txstring[txj];
      txj++;
      txstatus=3;
      rtty_txbit (0); // Start Bit;
      txi=0;
    }
    else 
    {
      txstatus=0; // Should be finished
      txj=0;
      count++;
    }
    break;
  case 3:
    if(txi<ASCII)
    {
      txi++;
      if (txc & 1) rtty_txbit(1); 
      else rtty_txbit(0);	
      txc = txc >> 1;
      break;
    }
    else 
    {
      rtty_txbit (1); // Stop Bit
      txstatus=4;
      txi=0;
      break;
    } 
  case 4:
    if(STOPBITS==2)
    {
      rtty_txbit (1); // Stop Bit
      txstatus=2;
      break;
    }
    else
    {
      txstatus=2;
      break;
    }

  }
}

void rtty_txbit (int bit)
{
  if (bit)
  {
    digitalWrite(MTX2_TXD,HIGH);
    //#ifdef APRS
//    analogWrite(MTX2_TXD, MTX2_OFFSET+((MTX2_SHIFT*4)/16)); // High
    //#endif
    //#ifndef APRS
    //    analogWrite(MTX2_TXD, MTX2_OFFSET+((MTX2_SHIFT*1.8)/16)); // High
    //#endif

  }
  else
  {
      digitalWrite(MTX2_TXD,LOW);
//    analogWrite(MTX2_TXD, MTX2_OFFSET); // Low
  }
}
void resetGPS() {
  uint8_t set_reset[] = {
    0xB5, 0x62, 0x06, 0x04, 0x04, 0x00, 0xFF, 0x87, 0x00, 0x00, 0x94, 0xF5           };
  sendUBX(set_reset, sizeof(set_reset)/sizeof(uint8_t));
}
void sendUBX(uint8_t *MSG, uint8_t len) {
  Serial.flush();
  Serial.write(0xFF);
  wait(100);
  for(int i=0; i<len; i++) {
    Serial.write(MSG[i]);
  }
}
void setupGPS() {
  // Turning off all GPS NMEA strings apart on the uBlox module
  // Taken from Project Swift (rather than the old way of sending ascii text)
  int gps_set_sucess=0;
  uint8_t setNMEAoff[] = {
    0xB5, 0x62, 0x06, 0x00, 0x14, 0x00, 0x01, 0x00, 0x00, 0x00, 0xD0, 0x08, 0x00, 0x00, 0x80, 0x25, 0x00, 0x00, 0x07, 0x00, 0x01, 0x00, 0x00, 0x00, 0x00, 0x00, 0xA0, 0xA9           };
  sendUBX(setNMEAoff, sizeof(setNMEAoff)/sizeof(uint8_t));
  while(!gps_set_sucess)
  {
    sendUBX(setNMEAoff, sizeof(setNMEAoff)/sizeof(uint8_t));
    gps_set_sucess=getUBX_ACK(setNMEAoff);
    if(!gps_set_sucess)
    {
      blinkled(2);
    }
  }
  wait(500);
  setGPS_GNSS();
  wait(500);
  setGPS_DynamicModel6();
  wait(500);
  setGps_MaxPerformanceMode();
  wait(500);
}

void setGPS_DynamicModel6()
{
  int gps_set_sucess=0;
  uint8_t setdm6[] = {
    0xB5, 0x62, 0x06, 0x24, 0x24, 0x00, 0xFF, 0xFF, 0x06,
    0x03, 0x00, 0x00, 0x00, 0x00, 0x10, 0x27, 0x00, 0x00,
    0x05, 0x00, 0xFA, 0x00, 0xFA, 0x00, 0x64, 0x00, 0x2C,
    0x01, 0x00, 0x00, 0x00, 0x00, 0x00, 0x00, 0x00, 0x00,
    0x00, 0x00, 0x00, 0x00, 0x00, 0x00, 0x16, 0xDC           };
  while(!gps_set_sucess)
  {
    sendUBX(setdm6, sizeof(setdm6)/sizeof(uint8_t));
    gps_set_sucess=getUBX_ACK(setdm6);
  }
}
void setGPS_GNSS()
{
  // Sets CFG-GNSS to disable everything other than GPS GNSS
  // solution. Failure to do this means GPS power saving 
  // doesn't work. Not needed for MAX7, needed for MAX8's
  int gps_set_sucess=0;
  uint8_t setgnss[] = {
    0xB5, 0x62, 0x06, 0x3E, 0x2C, 0x00, 0x00, 0x00,
    0x20, 0x05, 0x00, 0x08, 0x10, 0x00, 0x01, 0x00,
    0x01, 0x01, 0x01, 0x01, 0x03, 0x00, 0x00, 0x00,
    0x01, 0x01, 0x03, 0x08, 0x10, 0x00, 0x00, 0x00,
    0x01, 0x01, 0x05, 0x00, 0x03, 0x00, 0x00, 0x00,
    0x01, 0x01, 0x06, 0x08, 0x0E, 0x00, 0x00, 0x00,
    0x01, 0x01, 0xFC, 0x11   };
  while(!gps_set_sucess)
  {
    sendUBX(setgnss, sizeof(setgnss)/sizeof(uint8_t));
    gps_set_sucess=getUBX_ACK(setgnss);
  }
}
void setGPS_DynamicModel3()
{
  int gps_set_sucess=0;
  uint8_t setdm3[] = {
    0xB5, 0x62, 0x06, 0x24, 0x24, 0x00, 0xFF, 0xFF, 0x03,
    0x03, 0x00, 0x00, 0x00, 0x00, 0x10, 0x27, 0x00, 0x00,
    0x05, 0x00, 0xFA, 0x00, 0xFA, 0x00, 0x64, 0x00, 0x2C,
    0x01, 0x00, 0x00, 0x00, 0x00, 0x00, 0x00, 0x00, 0x00,
    0x00, 0x00, 0x00, 0x00, 0x00, 0x00, 0x13, 0x76           };
  while(!gps_set_sucess)
  {
    sendUBX(setdm3, sizeof(setdm3)/sizeof(uint8_t));
    gps_set_sucess=getUBX_ACK(setdm3);
  }
}
void setGps_MaxPerformanceMode() {
  //Set GPS for Max Performance Mode
  uint8_t setMax[] = { 
    0xB5, 0x62, 0x06, 0x11, 0x02, 0x00, 0x08, 0x00, 0x21, 0x91           }; // Setup for Max Power Mode
  sendUBX(setMax, sizeof(setMax)/sizeof(uint8_t));
}

boolean getUBX_ACK(uint8_t *MSG) {
  uint8_t b;
  uint8_t ackByteID = 0;
  uint8_t ackPacket[10];
  unsigned long startTime = millis();

  // Construct the expected ACK packet    
  ackPacket[0] = 0xB5;	// header
  ackPacket[1] = 0x62;	// header
  ackPacket[2] = 0x05;	// class
  ackPacket[3] = 0x01;	// id
  ackPacket[4] = 0x02;	// length
  ackPacket[5] = 0x00;
  ackPacket[6] = MSG[2];	// ACK class
  ackPacket[7] = MSG[3];	// ACK id
  ackPacket[8] = 0;		// CK_A
  ackPacket[9] = 0;		// CK_B

  // Calculate the checksums
  for (uint8_t ubxi=2; ubxi<8; ubxi++) {
    ackPacket[8] = ackPacket[8] + ackPacket[ubxi];
    ackPacket[9] = ackPacket[9] + ackPacket[8];
  }

  while (1) {

    // Test for success
    if (ackByteID > 9) {
      // All packets in order!
      return true;
    }

    // Timeout if no valid response in 3 seconds
    if (millis() - startTime > 3000) { 
      return false;
    }

    // Make sure data is available to read
    if (Serial.available()) {
      b = Serial.read();

      // Check that bytes arrive in sequence as per expected ACK packet
      if (b == ackPacket[ackByteID]) { 
        ackByteID++;
      } 
      else {
        ackByteID = 0;	// Reset and look again, invalid order
      }

    }
  }
}
uint16_t gps_CRC16_checksum (char *string)
{
  size_t i;
  uint16_t crc;
  uint8_t c;

  crc = 0xFFFF;

  // Calculate checksum ignoring the first two $s
  for (i = 5; i < strlen(string); i++)
  {
    c = string[i];
    crc = _crc_xmodem_update (crc, c);
  }

  return crc;
}

void blinkled(int blinks)
{
  for(int blinkledx = 0; blinkledx <= blinks; blinkledx++) {
    digitalWrite(LED_WARN,HIGH);
    wait(100);
    digitalWrite(LED_WARN,LOW);
    wait(100);
  }    
}    

void wait(unsigned long delaytime) // Arduino Delay doesn't get CPU Speeds below 8Mhz
{
  unsigned long _delaytime=millis();
  while((_delaytime+delaytime)>=millis()){
  }
}
uint8_t gps_check_nav(void)
{
  uint8_t request[8] = {
    0xB5, 0x62, 0x06, 0x24, 0x00, 0x00, 0x2A, 0x84           };
  sendUBX(request, 8);

  // Get the message back from the GPS
  gps_get_data();

  // Verify sync and header bytes
  if( buf[0] != 0xB5 || buf[1] != 0x62 ){
    GPSerror = 41;
  }
  if( buf[2] != 0x06 || buf[3] != 0x24 ){
    GPSerror = 42;
  }
  // Check 40 bytes of message checksum
  if( !_gps_verify_checksum(&buf[2], 40) ) {
    GPSerror = 43;
  }


  // Return the navigation mode and let the caller analyse it
  navmode = buf[8];
}
void gps_get_data()
{
  Serial.flush();
  // Clear buf[i]
  for(int i = 0;i<60;i++) 
  {
    buf[i] = 0; // clearing buffer  
  }  
  int i = 0;
  unsigned long startTime = millis();

  while ((i<60) && ((millis() - startTime) < 1000) ) { 
    if (Serial.available()) {
      buf[i] = Serial.read();
      i++;
    }
  }
}
bool _gps_verify_checksum(uint8_t* data, uint8_t len)
{
  uint8_t a, b;
  gps_ubx_checksum(data, len, &a, &b);
  if( a != *(data + len) || b != *(data + len + 1))
    return false;
  else
    return true;
}
void gps_ubx_checksum(uint8_t* data, uint8_t len, uint8_t* cka,
uint8_t* ckb)
{
  *cka = 0;
  *ckb = 0;
  for( uint8_t i = 0; i < len; i++ )
  {
    *cka += *data;
    *ckb += *cka;
    data++;
  }
}
void checkDynamicModel() {
  if(alt<=1000&&sats>4) {
    if(navmode != 3)
    {
      setGPS_DynamicModel3();
      errorstatus |=(1 << 3);  // Set Bit 3 indicating we are in pedestrian mode    
    }
  }
  else
  {
    if(navmode != 6){
      setGPS_DynamicModel6();
      errorstatus &= ~(1 << 3); // Unset bit 3 indicating we are in flight mode

    }
  }
}
void setGPS_PowerSaveMode() {
  // Power Save Mode 
  uint8_t setPSM[] = { 
    0xB5, 0x62, 0x06, 0x11, 0x02, 0x00, 0x08, 0x01, 0x22, 0x92           }; // Setup for Power Save Mode (Default Cyclic 1s)
  sendUBX(setPSM, sizeof(setPSM)/sizeof(uint8_t));
}
void prepare_data() {
  if(aprstxstatus==0)
  {
    sensors.requestTemperatures();
    temperature1=sensors.getTempCByIndex(0);
    if(tempsensors==2)
    {
      temperature2=sensors.getTempCByIndex(1);
    }
    if(temperature1==-127)
    {
      errorstatus |=(1 << 2); // Set bit 2 indicating the temp sensor is faulty
    }
    else
    {
      errorstatus &= ~(1 << 2); // Unset bit 2 indicating temp sensor is ok.
    }
  } 
  gps_check_lock();
  gps_get_position();
  gps_get_time();
  batteryadc_v=analogRead(BATTERY_ADC)*4.8;
  battvsmooth[4] = battvsmooth[3];
  battvsmooth[3] = battvsmooth[2];
  battvsmooth[2] = battvsmooth[1];
  battvsmooth[1] = battvsmooth[0];
  battvsmooth[0] = batteryadc_v;
  battvaverage = (battvsmooth[0]+battvsmooth[1]+ battvsmooth[2]+battvsmooth[3]+battvsmooth[4])/5;


}
void gps_check_lock()
{
  GPSerror = 0;
  Serial.flush();
  // Construct the request to the GPS
  uint8_t request[8] = {
    0xB5, 0x62, 0x01, 0x06, 0x00, 0x00,
    0x07, 0x16                                                                                                                                                                  };
  sendUBX(request, 8);

  // Get the message back from the GPS
  gps_get_data();
  // Verify the sync and header bits
  if( buf[0] != 0xB5 || buf[1] != 0x62 ) {
    GPSerror = 11;
  }
  if( buf[2] != 0x01 || buf[3] != 0x06 ) {
    GPSerror = 12;
  }

  // Check 60 bytes minus SYNC and CHECKSUM (4 bytes)
  if( !_gps_verify_checksum(&buf[2], 56) ) {
    GPSerror = 13;
  }

  if(GPSerror == 0){
    // Return the value if GPSfixOK is set in 'flags'
    if( buf[17] & 0x01 )
      lock = buf[16];
    else
      lock = 0;

    sats = buf[53];
  }
  else {
    lock = 0;
  }
}
void gps_get_position()
{
  GPSerror = 0;
  Serial.flush();
  // Request a NAV-POSLLH message from the GPS
  uint8_t request[8] = {
    0xB5, 0x62, 0x01, 0x02, 0x00, 0x00, 0x03, 0x0A           };
  sendUBX(request, 8);

  // Get the message back from the GPS
  gps_get_data();

  // Verify the sync and header bits
  if( buf[0] != 0xB5 || buf[1] != 0x62 )
    GPSerror = 21;
  if( buf[2] != 0x01 || buf[3] != 0x02 )
    GPSerror = 22;

  if( !_gps_verify_checksum(&buf[2], 32) ) {
    GPSerror = 23;
  }

  if(GPSerror == 0) {
    if(sats<4)
    {
      lat=0;
      lon=0;
      alt=0;
    }
    else
    {
      lon = (int32_t)buf[10] | (int32_t)buf[11] << 8 | 
        (int32_t)buf[12] << 16 | (int32_t)buf[13] << 24;
      lat = (int32_t)buf[14] | (int32_t)buf[15] << 8 | 
        (int32_t)buf[16] << 16 | (int32_t)buf[17] << 24;
      alt = (int32_t)buf[22] | (int32_t)buf[23] << 8 | 
        (int32_t)buf[24] << 16 | (int32_t)buf[25] << 24;
    }
    // 4 bytes of latitude/longitude (1e-7)
    lon_int=abs(lon/10000000);
    lon_dec=(labs(lon) % 10000000)/10;
    lat_int=abs(lat/10000000);
    lat_dec=(labs(lat) % 10000000)/10;


    // 4 bytes of altitude above MSL (mm)

    alt /= 1000; // Correct to meters
  }

}
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

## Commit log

2013-06-27 Initial Commit
    Initial Commit of the Habduino code & Eagle files
    [HABduino1.1.brd, HABduino1.1.sch]
2013-06-29 Updated BRD File + Added Sketchup Model
    1/ Removed GND via that linked VCC to GND (duh!)
    2/ Cleaned up silk screen.
    3/ Added location mark to TPS61200 module.
    4/ Added Sketchup Model
    [HABduino1.1.brd, HABduino1.1.sch, HABdunio.skp]
2013-07-02 Minor silk screen amendments
    [HABduino1.1.brd]
2013-07-18 Missing bstop & code mod
    Eagle board file was missing the bStop under the regulator making it
    very tricky to hand solder the TPS62100 module.
    Amended code in a number of places to remove aprs counter if not using
    APRS, switched warning LED's round.
    [HABduino1.1.brd]
2013-08-03 Updated error code description
    Put explanation of error codes in comments.
    [habduino.ino]
2013-08-12 Minor fix
    N_TXE was labelled N_TXD on the schematic. Fixed the net name.
2013-09-01 Amended frequency selection
    Removed the per channel frequency selection and replace it with very
    granular frequency selection using Daniel Richmans LMT2 N&R Calculation
    code
    [habduino.ino]
2013-10-09 Revert "Amended frequency selection"
    This reverts commit e987e9935bc74b5b7e79517ef354fd362f5e6a4e.
    [habduino.ino]
2013-10-09 Revert "Revert "Amended frequency selection""
    This reverts commit e42edad16fc68c9f1d338c9440661a7b8e9a1fb2.
    [habduino.ino]
2013-11-06 Bug fixes and amended location
    Fixed a bug where the NMEA strings weren't turning off which caused the
    rest of the packets from the GPS to fail checksums.
    Moved to habduino subdirectory to please Arduino when downloading.
    [habduino.ino]
2013-11-09 Fixed 2 bugs
    1/ https://github.com/HABduino/HABduino/issues/4
    2/ https://github.com/HABduino/HABduino/issues/5
    [habduino.ino]
2014-03-13 GPS Locking Bug
    Under certain circumstances GPS could lock up if antenna wasn't screwed
    on correctly and it had gone into PSM mode. Added code to put it back
    into max performance mode and eventually cold boot the GPS if having
    issues.
    Also added additional error bit 2 indicating an issue with temp sensor.
    Fixed warning LED blinking warning (now blinks at 1hz as expected when
    there is an error condition)
    Added battery voltage to telemetry
    Change status code to hex
    Changed default call sign to CHANGEME
    Removed some redundant variables
    [habduino.ino]
2014-03-25 Additional Features added
    1/ Automatically detects a secondary temperature sensor and adds to
    telemetry
    2/ Reports battery voltage and smooths it.
    3/ Amended disclaimer/information.
2014-04-06 Fixed some spacing issues in code
    Closing brackets were off the edge of the screen.
    [habduino.ino]
2014-04-12 Amended telemetry string construction code
    Avoids potential bugs
    [habduino.ino]
2014-05-16 Amended txstring length
    https://github.com/HABduino/HABduino/issues/9
    Max length is 90 :
    $$ABCDEFGHI,65535,99:99:99,-123.123456,-123.123456,65535,99,-123,-123,65535,65535,FF*FFFF
    Made txstring 100 long
    [habduino.ino]
2014-05-17 Fixed RTTY Shift Bug when using APRS
    1/ Fixed RTTY shift bug when using APRS.
    2/ Removed setPwmFrequency routine entirely.
    3/ Moved the APRS settings into ax25modem.h
    [habduino.ino]
2014-07-28 Bug fix
    Variable was set too small
    [habduino.ino]
2014-09-02 Revert "Bug Fix"
    This reverts commit 4f761bcb3b1ebe6875d95b780ed67466d98a066d.
    [habduino.ino]
2014-09-02 Revert "Bug fix"
    This reverts commit 715a86ef62abbb9d4fb7681befcacc71bd26ad42.
    [habduino.ino]
2014-10-28 New hardware version 3.0
    Removed LMT2 and replaced with MTX2 transmitter.
    Removed TO92 DS18B20 and replaced with SMD version.
    Removed Reset Protect + Reset switch
    Switch power supply +/- round to match the Pi In The Sky.
    Minor Silk Screen amendments.
    [HABduino3.0.brd, HABduino3.0.sch]
2014-11-04 Split scripts out into two versions
    V3 for the MTX2 based boards.
2014-11-04 Added Frequency Selection Code for MTX2
    Tuned shift setting for 425hz.
    Amended frequency selection code for MTX2
    Removed References to LMT2
2014-11-06 Added setGPS_GNSS
    MAX8's default to multi GNSS mode disabling power saving. Added code to
    disable all but GPS GNSS solutions. (Untested at this time)
2014-12-07 Bug in APRS Fixed
    APRS wasn't decoding correctly. Massive thanks to Phil Heron for noting
    the Temp sensor was glitching the APRS transmission.
    [habduino_v3.ino]
2015-12-09 Added V4.1 Hardware
    Added V4.1 Hardware
    [HABduino41.brd, HABduino41.sch]
2017-07-14 Fixed call sign length bug
    [habduino_v4.ino]

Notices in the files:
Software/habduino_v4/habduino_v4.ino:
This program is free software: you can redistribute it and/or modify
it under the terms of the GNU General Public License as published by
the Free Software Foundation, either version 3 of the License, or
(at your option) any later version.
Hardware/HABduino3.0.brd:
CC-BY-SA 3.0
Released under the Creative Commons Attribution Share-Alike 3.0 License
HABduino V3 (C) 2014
